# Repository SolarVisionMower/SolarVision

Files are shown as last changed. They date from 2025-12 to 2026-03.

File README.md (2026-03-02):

# SolarVision Mower

> [!NOTE]
> *This project is still in development!*

## Project Overview

SolarVision Mower is a YOLO and LiDAR based autonomous lawnmower that we're building for our final capstone engineering project. Once complete, it will feature *fully custom hardware and software*, which includes custom circuitry, firmware, 3D printed or welded components, a modified frame from an existing TORO lawnmower, and much more.

To stay up-to-date with the latest developments, check out the [dev/general][01] branch (specifically the [BACKLOG.md][02] file), to find a detailed list of everything we're doing. It will also help to navigate the various branches and directories (which will most likely grow in complexity as time progresses). Branches will the naming convention `xx/yy` are *permanent* branches, in the category specified by `xx`. Others can be considered temporary only.

## Tech Stack

- Software Tools
    - **KiCAD** - For PCB Design
    - **Fusion360** - For designing 3D models
    - **ESP-IDF** - For firmware programming on the ESP32
    - **STM32CubeMX** - For hardware configuration and initial code generation on the STM32
    - **STM32CubeIDE** - For firmware programming on the STM32
    - **ST Edge AI Suite** - For YOLO model conversion and code generation
- Software Libraries
    - **FreeRTOS** - For multithreading on both microcontrollers
    - **[espressif/arduino-esp32][05]** - For running Arduino functions in the ESP32
    - **[thijses/rplidar][06]** - For ease of integration of the RPLidar A1.
    - **[jh247247/DW1000-fan-video][07]** - Initial firmware implementation for the Ultra Wideband Positioning Modules
- Hardware Tools
    - Fabrication tools from the [NJIT Makerspace][08].
    - Circuit analysis tools from the [NJIT ECE Labs][09].
    - SLogic16U3 Logic Analyzer.
    - [JLCPCB][10] for PCB fabrication

## The Team

- Arnav Revankar
    - **Computer Engineer** - Graduating Dec 2026
    - Responsibilities:
        - Co-Lead Developer, and Manager for Hardware Design.
        - Developed the [STM32N6 Board][03]
        - Oversaw the development of the [Main Board][04]
- Panuha Were
    - **Computer Engineer** - Graduating May 2026
    - Responsibilities:
        - Co-Lead Developer, and Manager for Software Design
        - Contributed to the [Main Board][04] hardware design
        - Overseeing Firmware Development for the ESP32S3
- Layth Younes 
    - **Computer Engineer** - Graduating May 2026
    - Responsibilities:
        - Developer, and Manager for 3D Designs and Fabrication
        - Contributed to the [Main Board][04] hardware design
        - Overseeing the physical design of the frame, and enclosures.
- Daniel Assaf
    - **Computer Engineer** - Graduating May 2026
    - Responsibilities:
        - Developer, and Test/Integration Engineer
        - Contributed to the [Main Board][04] hardware design
        - Contributed to writing Documentation/Reports on progress.

## License

As of date (March 2nd, 2026) we have *not* decided upon a license. All rights are reserved by the authors.

<!-- Links -->
[01]: https://github.com/SolarVision/SolarVisionMower/tree/dev/general
[02]: https://github.com/SolarVision/SolarVisionMower/blob/dev/general/docs/BACKLOG.md
[03]: https://github.com/SolarVision/SolarVisionMower/tree/dev/PCBDesign/Hardware/STM32N6_Board
[04]: https://github.com/SolarVision/SolarVisionMower/tree/dev/MainBoard/Hardware/Main_Board
[05]: https://github.com/espressif/arduino-esp32
[06]: https://github.com/thijses/rplidar
[07]: https://github.com/jh247247/DW1000-fan-video
[08]: https://njitmakerspace.com
[09]: https://ecelabs.njit.edu
[10]: https://jlcpcb.com

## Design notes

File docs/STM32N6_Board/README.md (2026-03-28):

# STM32N6 Board

Documentation for all components to be used on the board.

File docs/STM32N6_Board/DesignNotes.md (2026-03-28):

# Design Notes

## Ballout

- This section was completed *after* wiring the Power and Analog units, as well as the NOR Flash unit in the schematic. However it is important, so it'll be at the top.
- There's a spreadsheet for the BGA pinout, can be found [here](https://docs.google.com/spreadsheets/d/1W3wl7rZQ2mxVOFGO9Ns9zJrD_qd8Au_sG3PKxmy8APU/edit?usp=sharing). It has *all* the balls, but the ones we need have been checked off, and most have signals labeled next to them.
- The pinout was generated in STM32CubeMX, and the configuration has been stored in [`Software/`](../../Software).
- The ballout from the CubeMX's UI is shown below. It isn't very detailed in the photo, so consulting the spreadsheet (or better, git pull and open in CubeMX) is highly recommended.

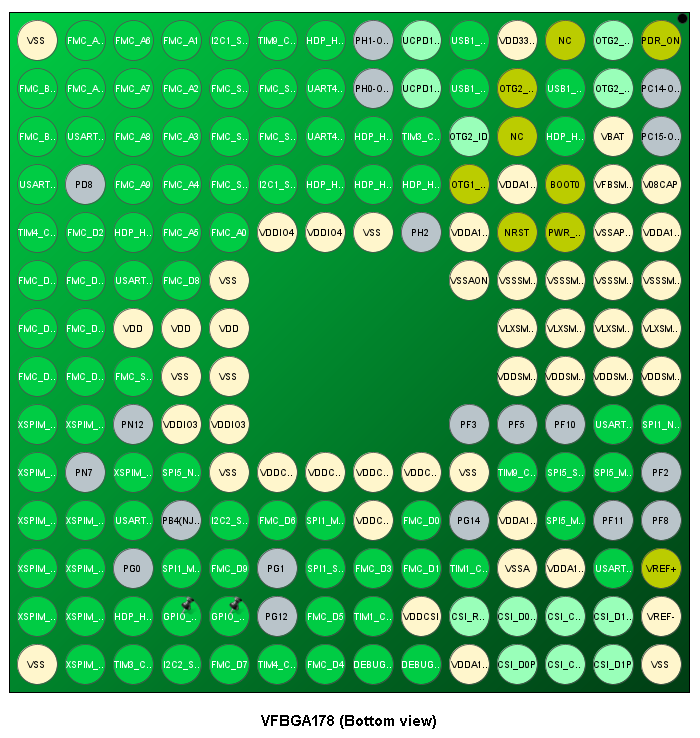
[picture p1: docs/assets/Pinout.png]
Ballout from STM32CubeMX


The STM32's **connection with the main board** will be through a set of two 18 pin header pins on each side of the stm32. These pins will be as follows, top to bottom:

| Left | Right |
|:----:|:-----:|
| 5V | 5V |
| GND | GND |
| UART1-TX | UART2-TX |
| UART1-RX | UART2-RX |
| UART3-TX | UART4-TX |
| UART3-RX | UART4-RX |
| SPI1-MISO | SPI5-MISO |
| SPI1-MOSI | SPI5-MOSI |
| SPI1-CS | SPI5-CS |
| SPI1-CLK | SPI5-CLK |
| I2C1-SDA | I2C2-SDA |
| I2C1-SCL | I2C2-SCL |
| TIM1-CH1 | TIM3-CH2 |
| TIM1-CH2 | TIM3-CH3 |
| TIM4-CH1 | TIM9-CH1 |
| TIM4-CH2 | TIM9-CH2 |
| 5V | 5V |
| GND | GND |

- Putting 5V *and* ground on each side promotes better current flow through the ground planes I believe. This will allow charges to flow in the direction to the nearest ground.
- 5V pins will have reverse polarity protection diodes.
- All pins are technically GPIO pins, but they can also be used specifically for the tasks displayed. The timer pins are capable of PWM, and analog read upto 1v8.

## Power

- VDD has 7 capacitors because:
    - 3 VDD pins
    - 2 VDDIO3 pins
    - 2 VDDIO4 pins
- VDDCORE has 6 capacitors because:
    - 5 VDDCORE pins
    - 1 VDDCSI pin
- VDDA1V8 has 4 capacitors because:
    - ADC, CSI, USB, and PLL power
- ***NOTE:*** In PCB design, keep decoupling capacitors close to the BGA chip.

- Notes on Power Pinout:
    - Will obviously need a ground pin or two
    - Input voltage pin will be 5V, with a max of 3A consumption (Buck converter on main board). Use IPC-2221 to determine trace widths. 
        - The hardware development AN suggests using a 4 (if not 6) layer PCB with the inner layers being strictly ground and power planes.
    - V\_DD and V\_DDA18AON ***need to start first*** according to the boot order. The rest of the pins can be powered after. Thus:
        - V\_DD and V\_DDA18AON must be powered off two *separate* (crucial for analog signal integrity) LDO's.
        - V\_DDA1V8 will then be powered by an LDO off of the 5V input, *with PWR\_ON on the enable pin*.
        - V\_DD1V8 and V\_DD3V3 should be powered by buck converters off 5V for high power. Again *PWR\_ON TO ENABLE PIN*.
    - V\_DDA1V8PMU is powered off V\_DD1V8, with 50R@100MHz ferrite and 100n bypass cap in between.

## Analog Unit

- USB:
	- DP and DM are differential pairs, with 90 Ohms between them, or 45 Ohms each between them and ground.
	- Length matching within a pair should be within 2mm, and maximum trace length no longer than 200mm.
	- Ideally route DP and DM over a ground plane.
	- Using the ECM42-40A100N6 to filter noise.
	- Both CC pins have been pulled down. To change configuration, unsolder R24 or R25.
	- USB Power Details:
		- When connected to a host via USB C, VBUS will be able to power 5V via the diode D5. 
		- When *acting* as a USB host (`EN = 1`), the NMOS will enable VBUS to be powered by 5V.
		- If connected to a host, but also powered by 5V rail, VBUS and 5V will be powered separately, *but to the same voltage*, so theoretically I\_D should be 0.
		- Same situation as above if acting as a host, and for some reason a device supplies 5V on VBUS
		- If, for any reason, there's a flaw in this design, **unsoldering D5** should fix it, but external powering capabilities will vanish.
- CSI
	- The 3 pairs of P and N pins for the CSI peripheral are also *differential pairs*. There's 100 Ohms impedance between them, and 50 Ohms between each of them and ground.
	- Length matching within a pair must be within 0.1mm, and between clock and data pairs 2.5mm.
	- Route over a ground plane.
	- Trace lengths must not exceed 200mm.
- General
	- NRST is internally pulled up via 40k Ohms. Thus, the button debouncing cap will have a H-L time constant of 1ms, and L-H of 4ms.
	- NRST will also be connected to a GPIO, which one is to be determined.

## XSPI NOR Flash

- Pin configurations
	- Uses pins PN[0..12]
	- CS is active low, on pin PN1
	- CLK is on PN6
	- DQS (Data Strobe) is on pin PN0
	- Serial IO pins are on PN[2..5] and PN[8..11]
	- 3V supply by separate LDO using label VDD_OCTO
- Capacitors should be placed close to supply pins, in pairs of 4.7u and 100n.
- SIO pins to be length matched to within 10mm (I say 1-5mm), and impedance matched to 50 Ohms between trace and ground.
- Differential pairs must have trace impedance of 100Ohms between them.
- Trace capacitance not to exceed 20pF, and trace length not to exceed 120mm (use resistor termination otherwise; not doing this).
- External push button to reset the Flash. Once development is complete, R28 can be unsoldered to prevent accidentally deleting data.
- NRST connected to the reset button through a diode.

## PCB Design

- Impedance controlled traces:
	- For 50 Ohms single ended, 0.1565mm
	- For 45 Ohms single ended, 0.1933mm
	- For 100 Ohms diff pair, 50 Ohms single ended, 0.15mm wide, 0.5mm spacing, > 2mm gap to ground plane
	- For 90 Ohms diff pair, 45 Ohms single ended, 0.19mm wide, 0.5mm spacing, > 2mm gap to ground plane

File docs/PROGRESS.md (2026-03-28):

# PROGRESS

Documentation of all development across all branches.

[Link to BACKLOG.md](./BACKLOG.md)

> [!NOTE]
> Upon merging a development branch into this branch (`dev`), update the Completed section with the latest developments,
> and *in the proper format!* This format is `<Completed Task> - <Merged By> - <Date> - <Commit Hash>`

## TODO

- **Physical Design**
	- Designing the Frame
	- Welding the Frame
	- Attaching and Testing Components
	- Building the Battery
- **PCB Design**
	- Main Board Design
	- Power Board Design (TBD)
	- STM32N6 Board Design
- **Programming**
	- Preliminary ESP32 Programming (FreeRTOS)
	- Interfacing ESP32 with LiDAR + UWB
	- Model Conversion and C Code Generation
	- Preliminary SLAM Code Testing
	- Path Planning Code Testing
	- Mower State Monitor on RbPi

## IN PROGRESS

- **PCB Design**
	- STM32N6 Board Design
		- Added all footprints, and symbols for MX25LM, IS42, and STM32
		- Added symbols for SPX5205 LDO, and MC34064 Buck. Standard footprints.
		- Completed Power and Analog Units of schematic, as well as MX25LM NOR Flash
		- Completed pinout process in STM32CubeMX. Completed pinout is [here](https://docs.google.com/spreadsheets/d/1W3wl7rZQ2mxVOFGO9Ns9zJrD_qd8Au_sG3PKxmy8APU/edit?usp=sharing).
		- Completed schematic layout, ERC check, and footprint assignment. Next is PCB layout.

## COMPLETED

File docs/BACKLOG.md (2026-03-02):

# BACKLOG

> [!IMPORTANT]
> Try not to commit to this branch! Commit in one of the sub-branches (ie `dev/xyz`) and merge as necessary

## Links to Branches

- [dev/PhysicalDesign](https://github.com/SolarVisionMower/SolarVision/tree/dev/PhysicalDesign)
- [dev/PCBDesign](https://github.com/SolarVisionMower/SolarVision/tree/dev/PCBDesign)
- [dev/DataCollection](https://github.com/SolarVisionMower/SolarVision/tree/dev/DataCollection)
- [dev/Programming](https://github.com/SolarVisionMower/SolarVision/tree/dev/Programming)
- [dev/Testing](https://github.com/SolarVisionMower/SolarVision/tree/dev/Testing)
- [dev/Shed](https://github.com/SolarVisionMower/SolarVision/tree/dev/Shed)
- [dev/Redocking](https://github.com/SolarVisionMower/SolarVision/tree/dev/Redocking)

## Major Tasks

Detailed list of everything to be done, in chronological order. It should be as detailed as possible; update here and in [PROGRESS.md](./PROGRESS.md) if anything's missing.

<details>
<summary>Physical Design</summary>

Design and build of the mower's frame; all development will be in the `dev/PhysicalDesign` branch.

As of Jan 17th 2026, we have yet to discuss details about the physical design. However, the general outline will be as follows:

- Begin with a base mower, and weld/rivet on L-bracket extensions on all four corners
- On top of L-bracket posts, weld more L-brackets to form a rectangular shape
- On top of the created base, mount aluminum extrusions as needed, and weld extensions for the wheels and rear motors. [Here is some inspiration](https://youtube.com/shorts/RLpBBrU3Dhs).
- Once electronics is complete, design and 3D print enclosures for the electronics.

Along with this, we will need to build a 10S 4P battery pack out of 18650 batteries. There is also the option of purchasing a pre-built battery, but that choice will come down to cost-balance, and is yet to be discussed (01/19/2026).
</details>

<details>
<summary>PCB Design</summary>

> [!IMPORTANT]
> Please place ***ALL DOCUMENTATION*** (datasheets, reference manuals, etc.) in their respective folders under the `docs` directory.
> All designs must be based off previous designs or specs from datasheets.

All development should be in the `dev/PCBDesign` branch.

There are 3 boards which we will need to design, order, and assemble:

- STM32N6 Board
    - This will be a 4 layer board, designed in KiCAD.
    - Will use an **STM32N657I0H3Q**
        - VFBGA178 Ballout
        - 0.8mm Pitch
        - 106 I/Os (not all used; perhaps only 20, others in internal pull-down state)
        - Comm Protocols we will use:
            - UART, for communication with the ESP32
            - I2C and SPI, for collecting sensor data
            - MIPI CSI-2, for camera connection
            - XSPI, for interfacing Macronix MX25LM51245GXDI00 NOR Flash (used for boot and binary storage), same as [the Nucleo-144 board](https://www.st.com/resource/en/schematic_pack/mb1940-n657x0q-c02-schematic.pdf)
            - (*IF TIME PERMITS*) FMC_SDRAM16, for interfacing IS42S16800F-7TLI SDRAM chip, to store YOLO weights. Otherwise, use system memory with YOLOv8-nano.
            - (*IF TIME PERMITS*) FMC Display Interface, for on-board monitoring. Not needed at all, since we'll have the web-UI.
        - Of the above, CSI, XSPI, and FMC_SDRAM will have dedicated connectors on the board, while the rest will have header pins to connect to the main control board.

- Main Control Board
    - This board will house the STM32N6 board, as well as an ESP32 S3, UWB Tag, and 433MHz RF module. MCU boards connected via header pins.
    - It will be a 2-layer board for simplicity
    - Will also house LDO regulators to deliver 1.8, 3.3, and 5V respectively, powering the ESP32 and STM32
    - Within the board:
        - Route UART between the boards
        - Route *all* ESP32 pins to the main board's header pins
        - Route I2C, SPI, FMC Display, and few extra I/O pins (TBD) from STM32 to the main board's header pins

- Power Board
    - ***NOTE:*** Necessity of this board is up to debate, as off-the-shelf power components are already available, and there's an added risk of errors in our designs. **TO BE DISCUSSED (01/19/2026)**
    - This board will power the **motors, lights, and other high-power electronics**
    - This board shall have *no MCU*; all control goes directly from main board to power board.
    - Connection to main board will be through either ribbon cable, or unseparated header pin cables (resembles ribbon cable)
</details>

<details>
<summary>Data Collection/Training</summary>

> [!NOTE]
> Since this is a *software* related portion of the project, try to use dockerized tools, if applicable

All development will be in the `dev/DataCollection` branch.

The YOLOv8 model running on the STM32 will be a fine-tuned segmentation model. Our goal is that it'll be able to detect grass vs non-grass, based on input from the camera. In order to do this, we must *collect training data*, and then *train* the model on a GPU. Current plan is as follows:

- Collect 300 to 400 images of a lawn, from a camera 2 feet in the air, parallel with the earth.
- Manually annotate all the images using Label Studio
- Load dataset into Google Colab, write training script, and train for ~100 epochs.
- Export model to `pt`, use PyTorch to quantize to INT8, and export to ONNX
- Finally, utilize ST Edge AI Core to [generate C code](https://stm32ai-cs.st.com/assets/embedded-docs/stneuralart_getting_started.html), then compile in STM32Cube IDE and flash.
- Test model accuracy
</details>

<details>
<summary>Programming</summary>

> [!NOTE]
> Since this is a *software* related portion of the project, try to use dockerized tools, if applicable.
> Also, try to write *modular* code, which can be improved upon at any instance.

All development will be in the `dev/Programming` branch.

Below is how we anticipate control flow within our entire project:

- STM32
    - Camera frame is captured and processed, creating segmented frame.
    - Mask of mower's current trajectory is mapped onto the segmented frame. 
    - Finally, logic (that we've yet to define) determines distance to the lawn's boundary, if applicable.
    - Results are sent to the ESP32 via UART
    - Mower state received from ESP32 is then displayed on FMC display, or sent to Raspberry Pi base station using the 433MHz RF module.
- ESP32
    - Utilize FreeRTOS for multithreading
    - ESP32 receives distance-to-boundary predictions, and replies with the current state of the mower:
        - Position, Speed, trajectory (steering angle), Blade motor RPM, and power consumption (if possible)
        - Sent using CSV format over UART
        - Parity checker to ensure data's integrity
    - Collects sensor data from LiDAR and UWB/GPS (preferably UWB Trilateration, from other open source projects), and integrates into SLAM system.
- SLAM
    - This portion is still slightly TBD
    - Keep track of mower's position, and update in an infinite loop.
    - At beginning of mowing cycle, use path-planning algorithm to set up waypoints at boundaries of the lawn. 
    - Travel to waypoints, simultaneously updating SLAM location and map. Once boundary is detected, turn around and drive back.
- Web-UI
    - Raspberry Pi base station will run a web server and API endpoint using Python, or some other tool, TBD.
</details>

<details>
<summary>Testing</summary>

All development will be in the `dev/Testing` branch (if necessary).

This will include testing of the following (if not already done, should be already done actually):

- Motors:
    - Make sure motors run, and the ESP32 can control them as designed.
- Vision System
    - Make sure the STM32 is able to receive data from the CSI camera, is able to process it, and generate accurate results. This is crucial
- LiDAR System
    - Make sure the ESP32 is able to receive data from the LiDAR sensor, and is able to process it into the SLAM map
- UWB Positioning System
    - Make sure it can calculate position based on distance from 2 anchors. 
    - Make sure it can process current position into SLAM model.
- SLAM
    - Make sure SLAM is effectively able to update its map and position, and send commands in order to reach waypoints, in a perpetual loop.
</details>

<details>
<summary>Shed Building</summary>

All development will be in the `dev/Shed` branch.

At this point, we will know the dimensions of the mower, and will be able to construct the shed. General steps will be:

- Build/buy shed
- Install solar panels
- Install MPPT charge controller with lead acid batteries
- Permanently install Raspberry Pi Base Station, and UWB anchors.
</details>

<details>
<summary>Re-docking Programming</summary>

All development will be in the `dev/Redocking` branch.

(*IF TIME PERMITS*)

Add functionality to the code to be able to detect and return to the docking station.
</details>

## Timeline

There are 4 of us team members, and so we will be splitting up responsibilities, setting deadlines, and holding each other accountable for said deadlines. Which team member performs which tasks has not been decided yet (01/19/2026), and thus they are referred to as Member #1, #2, #3, and #4 until we have reached a consensus. Roles have been distributed as evenly as possible.

[Budgeting spreadsheet can be found here.](https://drive.google.com/drive/folders/1ZBdfXEnTgUfjmxBh2aHWwEIxdO-Y8bWZ?usp=sharing)

**Edit (01/24/2026):** We have reached a consensus on the division of responsibilities. The Gantt Chart we created can be [found here](https://docs.google.com/spreadsheets/d/1--nTUD_fsUKMP01lJ4NdwEQdVoJq4U2uNLm4wrHddHY/edit?usp=sharing).

<!--
Table Template

| Task | Member \# | **Deadline** |
|:----:|:---:|:---:|
|  |  |  |
-->

- **Physical Design**

| Task | Member \# | **Deadline** |
|:----:|:---:|:---:|
| Welding the Frame | 1 | Feb 1 |
| Attaching physical components | 1 | Feb 8 |
| Testing DC Motors, and mower function | 1 | Feb 8 |
| Designing and 3D printing enclosures | 2 | TBD |
| Designing and Building 10S4P 18650 Battery | 1 | Feb 15 |

- **PCB Design**

| Task | Member \# | **Deadline** |
|:----:|:---:|:---:|
| Main Board Design, Validate, and Order | 2 | Feb 1 |
| Power Board Design, Validate, and Order (TBD) | 2 | Feb 8 |
| STM32N6 Board Design, Validate, and Order | 3 | Feb 1 |

- **Data Collection/Training**

| Task | Member \# | **Deadline** |
|:----:|:---:|:---:|
| Collecting Pictures | 3 | Feb 4 |
| Preliminary Training | 3 | Feb 11 |
| Testing/Iterations | 3 | Feb 21 |

- **Programming**

| Task | Member \# | **Deadline** |
|:----:|:---:|:---:|
| Preliminary ESP32 Programming (FreeRTOS) | 4 | Feb 1 |
| Interfacing ESP32 with LiDAR + UWB | 4 | Feb 8 |
| Model Conversion and C code generation | 4 | Feb 18 |
| C code assimilation + YOLO testing on N6 | 3 | Feb 21 |
| Preliminary SLAM Code Testing | 2 | Feb 28 |
| Path planning code testing | 2 | March 7 |
| Mower State Monitor on RbPi | 1 | Feb 28 |

- **Testing**

| Task | Member \# | **Deadline** |
|:----:|:---:|:---:|
| Testing Physical Components | 1 | March 7 |
| Testing ESP32 | 2 | March 14 |
| Testing STM32 | 3 | March 7 |
| Testing Communication, Web-UI, and overall mower function | 1, 2, 3, 4 | March 25 |

- **Shed Building**

| Task | Member \# | **Deadline** |
|:----:|:---:|:---:|
| Constructing Shed | 4 | April 1 |
| Installing Solar Panels | 4 | April 7 |
| **Senior Design Showcase Qualifications** | -- | April 7 |
| Installing MPPT Charge Controller, stationary battery pack, and mower charger | 4 | April 14 |

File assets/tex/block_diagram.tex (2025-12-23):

\usepackage{extarticle}
\documentclass[14pt]{extarticle}
\usepackage[paperheight=7in, paperwidth=10in, total={9.5in, 6.5in}]{geometry}
\usepackage{tikz}

\usetikzlibrary{automata, positioning, shapes.geometric, arrows.meta}

\tikzset{
    state/.style={
        ellipse, draw, fill={rgb:black,1;white,5},
        minimum size=10pt
    },
    box/.style={
        rectangle, draw, fill={rgb:black,1;white,5},
        minimum width=75pt, minimum height=50pt, align=center,
        anchor=north
    },
    mm/.style={
        -{Stealth[length=3mm]}
    },
    oo/.style={
        {Stealth[length=3mm]}-{Stealth[length=3mm]}
    },
    tikkup/.style={
        anchor=south west, rotate=20, align=left
    },
    tikkdown/.style={
        anchor=north east, rotate=20, align=right
    }
}

\begin{document}

\begin{center}
    {\Huge \bf Block Diagram of Autonomous Lawnmower} \\[45pt]
    \begin{tikzpicture}[x=5pt, y=5pt]
        % \draw[help lines, step=5] (0,0) grid (130,90);
        % \node at (0,0) {O};
        
        \node[box, minimum height=200pt, minimum width=125pt]   (mcu)           at (65,60) {STM32N6 MCU\\for YOLO Inference\\\\and\\\\ESP32 S3\\SLAM pathfinding\\and system control};

        % Navigation system
        
        \node[box] (autonomous)    at (35,65) {Autonomous\\Navigation\\System};
        \node[box] (gps)           at (10,65) {GPS/RTK\\Module};
        \node[box] (lidar)         at (10,80) {LiDAR\\Module};
        \node[box] (computer)      at (35,80) {Camera};

        \path (autonomous) edge[mm, out=0, in=180] (52,50)
                (gps) edge[mm] (autonomous)
                (lidar) edge[mm] (autonomous)
                (computer) edge[mm] (autonomous);

        % Blade speed control

        \node[box] (speedcontrol)   at (95,65)  {Blade Speed\\Control (PID)};
        \node[box] (speedsensor)    at (95,80)  {Blade Speed\\Sensor};
        \node[box] (blademotor)     at (120,65) {Blade Motor};

        \path (85,58) edge[mm, out=180, in=0] (78,48)
                (78,52) edge[mm, out=0, in=180] (85,62)
                (speedcontrol) edge[mm] (blademotor)
                (speedsensor) edge[mm] (speedcontrol);

        % Mower height control

        \node[box] (heightcontroller)   at (95,45)  {Mower Height\\Motor Controller};
        \node[box] (heightmotor)        at (120,45) {Mower Height\\Motor};

        \path (78,40) edge[mm] (heightcontroller)
                (heightcontroller) edge[mm] (heightmotor);

        % RF Modules

        \node[box] (transmitter)    at (95,25)  {RF Module};

        \path (78,28) edge[mm, out=0, in=180] (87,18)
                (87,22) edge[mm, out=180, in=0] (78,32);

        % Motors and Motor Controllers

        \node[box] (leftcontrol)    at (35,45) {Left Motor\\Controller};
        \node[box] (leftmotor)      at (10,45) {Left Motor};
        \node[box] (rightcontrol)   at (35,25) {Right Motor\\Controller};
        \node[box] (rightmotor)     at (10,25) {Right Motor};

        \path (52,40) edge[mm] (leftcontrol)
                (leftcontrol) edge[mm] (leftmotor)
                (52,30) edge[mm, out=180, in=0] (rightcontrol)
                (rightcontrol) edge[mm] (rightmotor);
    \end{tikzpicture}
\end{center}
    
\end{document}

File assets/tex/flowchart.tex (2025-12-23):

\usepackage{extarticle}
\documentclass[14pt]{extarticle}
\usepackage[paperheight=8.7in, paperwidth=11in, total={10.5in, 8.2in}]{geometry}
\usepackage{tikz}

\usetikzlibrary{automata, positioning, shapes.geometric, arrows.meta}

\tikzset{
    state/.style={
        ellipse, draw, fill={rgb:black,1;white,5},
        minimum size=10pt
    },
    mm/.style={
        -{Stealth[length=3mm]}
    },
    oo/.style={
        {Stealth[length=3mm]}-{Stealth[length=3mm]}
    },
    tikkup/.style={
        anchor=south west, rotate=27, align=left
    },
    tikkdown/.style={
        anchor=north east, rotate=27, align=right
    }
}

\begin{document}

\begin{center}
    {\Huge \bf Flowchart for Project Completion} \\[15pt]
    \begin{tikzpicture}[x=5pt, y=5pt]
        %\draw[help lines, step=5] (0,-30) grid (130,65);
        
        \node[state] (start)        at (65,60) {Start};
        
        \node[state] (SolarShed)    at (30,50) {Solar Shed};
        \node[state] (Shed)         at (10,40) {Shed};
        \node[state] (SolarPanel)   at (45,40) {Solar Panel};
        \node[state] (Battery)      at (15,23) {Battery};
        \node[state] (BMS)          at (45,23) {BMS};
        
        \node[state] (SystemBench) at (95,50) {System Bench-Test};

        \node[state] (Lidar)        at (70,40) {Lidar};
        \node[state] (GPS)          at (95,40) {GPS/RTK};
        \node[state] (YOLO)         at (120,40) {YOLO};
        % \node[state] (Triangle)     at (120,40) {Triangulation};

        \node[state, align=center] (Interface1)     at (70,23) {Interface\\w/ STM32};
        \node[state, align=center] (Interface2)     at (95,23) {Interface\\w/ STM32};
        \node[state, align=center] (Interface3)     at (120,23) {Interface\\w/ STM32};

        \node[state, align=center] (Navigation) at (95,7) {On-board ESP32 S3\\for Navigation};

        \node[state, align=center] (physical) at (35,7) {Physical Design\\+ Reiterations};

        \node[state] (complete) at (65,-5) {Completed Project};

        \path (start) edge[mm, out=180, in=30] (SolarShed)
                (SolarShed) edge[mm, out=180, in=90] (Shed)
                (SolarShed) edge[mm, out=0, in=90] (SolarPanel)
                (SolarPanel) edge[mm, out=180, in=90] (Battery)
                (SolarPanel) edge[mm] (BMS)
                (start) edge[mm, out=0, in=150] (SystemBench)
                (SystemBench) edge[mm, out=-180, in=90] (Lidar)
                (SystemBench) edge[mm] (GPS)
                (SystemBench) edge[mm, out=0, in=90] (YOLO)
                %(SystemBench) edge[mm, out=0, in=90] (Triangle)
                (Lidar) edge[mm] (Interface1)
                (GPS) edge[mm] (Interface2)
                %(Triangle) edge[mm] (Feasible)
                %(Feasible) edge[mm, line width=2pt, dash pattern={on 6pt off 4pt}, out=-90, in=20] (Navigation)
                (YOLO) edge[mm, out=-90, in=90] (Interface3)
                (Interface3) edge[mm, out=-90, in=0] (Navigation)
                (start) edge[-, out=-120, in=90] (58,40)
                (58,40) edge[-, out=-90, in=90] (58,25)
                (58,25) edge[mm, out=-90, in=45] (physical)
                (physical) edge[mm, out=-90, in=180] (complete)
                (Navigation) edge[mm, out=-90, in=0] (complete)
                (Interface1) edge[mm, out=-90, in=180] (Navigation)
                (Interface2) edge[mm] (Navigation)
                (BMS) edge[mm, out=-90, in=90] (physical)
                (Battery) edge[mm, out=-90, in=170] (physical)
                (Shed) edge[-, out=-130, in=90] (5,25)
                (5,25) edge[mm, out=-90, in=180] (physical); 

        \draw[oo] (10,-20) -- (120,-20);

        % \node at (0,0) {O};
        
        \draw[-] (15,-19) -- (15,-21);
        \draw[-] (115,-19) -- (115,-21);
        \draw[-] (27.5,-19) -- (27.5,-21);
        \draw[-] (65,-19) -- (65,-21);
        \draw[-] (40,-19) -- (40,-21);
        \draw[-] (52.5,-19) -- (52.5,-21);
        \draw[-] (90,-19) -- (90,-21);
        \draw[-] (102.5,-19) -- (102.5,-21);

        \node[tikkup] at (15,-19) {\bf Sept. 2025};
        \node[tikkup] at (115,-19) {\bf May 2025};
        \node[tikkup] at (27.5,-19) {\bf Present\\\bf Oct. 2025};
        \node[tikkup] at (65,-19) {\bf Jan. 2026};
        \node[tikkup] at (40,-19) {\bf Nov. 2025};
        \node[tikkup] at (52.5,-19) {\bf Dec. 2025};
        \node[tikkup] at (90,-19) {\bf March 2026};
        \node[tikkup] at (102.5,-19) {\bf Apr. 2026};

        \node[tikkdown] at (40,-21) {\bf Begin Solar Shed,\\\bf Battery, and BMS};
        \node[tikkdown] at (52.5,-21) {\bf Begin Bench Test};
        \node[tikkdown] at (65,-21) {\bf Begin Navigation System};
        \node[tikkdown] at (90,-21) {\bf Begin Physical Design};

        \path (102.5,-20) edge[out=-90, in=90] (108.75,-23)
                (108.75,-23) edge[out=90, in=-90] (115,-20);

        \node at (108.75,-25) {\bf Buffer Period};
    \end{tikzpicture}
\end{center}
    
\end{document}

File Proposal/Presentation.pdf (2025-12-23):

# SolarVision Mower: Autonomous Solar-Powered Lawn Maintenance

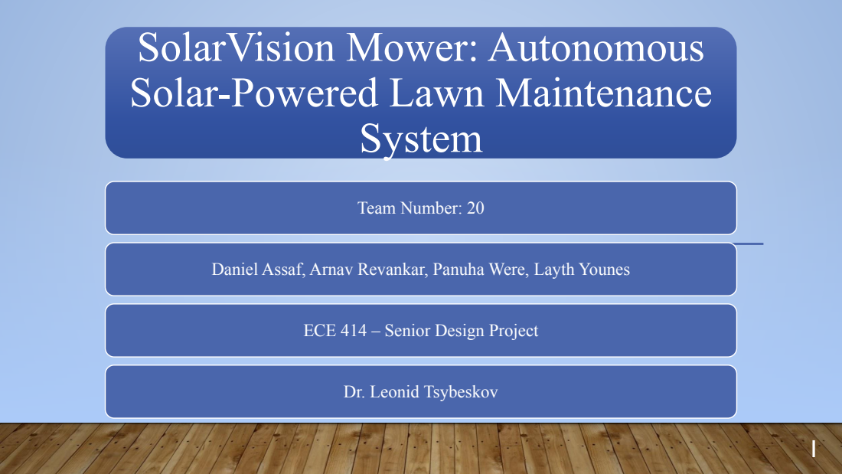
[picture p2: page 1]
System; Team Number: 20

Daniel Assaf, Arnav Revankar, Panuha Were, Layth Younes

ECE 414 – Senior Design Project

Dr. Leonid Tsybeskov

# Abstract

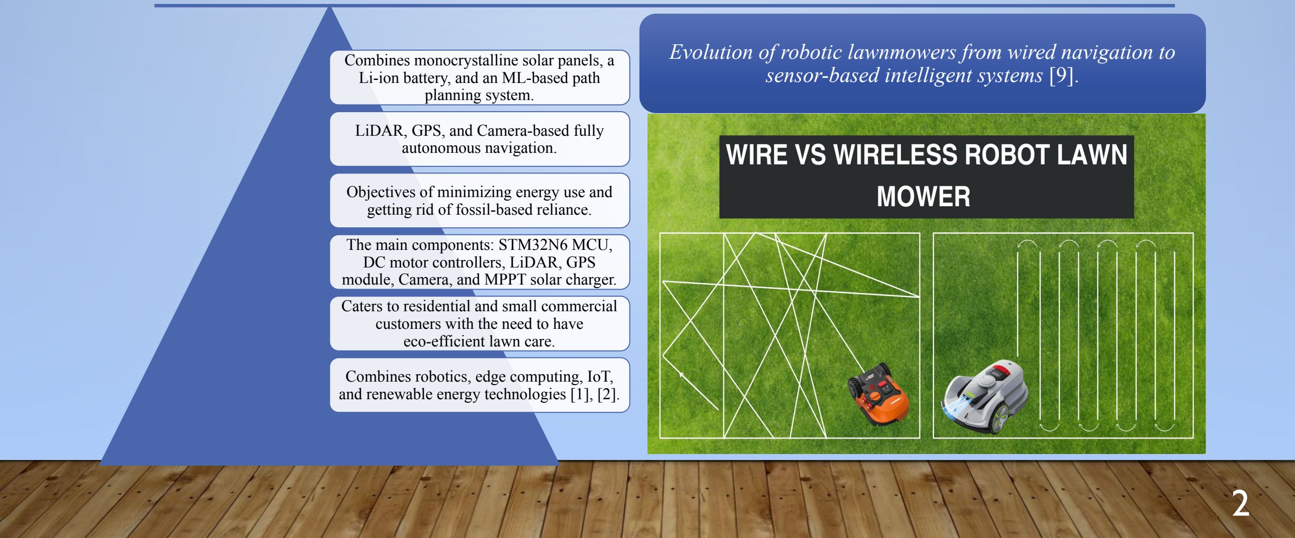
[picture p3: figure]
Combines monocrystalline solar panels, a Li-ion battery, and an ML-based path planning system.; LiDAR, GPS, and Camera-based fully autonomous navigation.; Objectives of minimizing energy use and getting rid of fossil-based reliance.; The main components: STM32N6 MCU, DC motor controllers, LiDAR, GPS module, Camera, and MPPT solar charger.; customers with the need to have eco-efficient lawn care.; Combines robotics, edge computing, IoT,; sensor-based intelligent systems [9].

Caters to residential and small commercial

and renewable energy technologies [1], [2].

## Evolution of robotic lawnmowers from wired navigation to

Part 1 Design Objectives,
Specifications, and Constraints.
- To create a completely independent solar-powered mower that can work throughout the day.

Objective 1:

- LiDAR, GPS, and Camera based SLAM
Objective 2: | obstacle avoidance and path planning
- Mobile/Web interface to monitor mower’s status and operation Objective 3:
- 3 12V monocrystalline solar panels, 36 V 10Ah Li-ion battery (10S 4P config). Power supply:
- ~1.5 hours on full charge, assuming 200W power consumption Hours of average run-time:
- Enclosure, slow control (less than 2 mph), boundary enforcement, and tilt detection. Safety limitations:
Budget constraint: | • Prototype should not go above $600.

## Proposed SolarVision Mower and its docking deck models

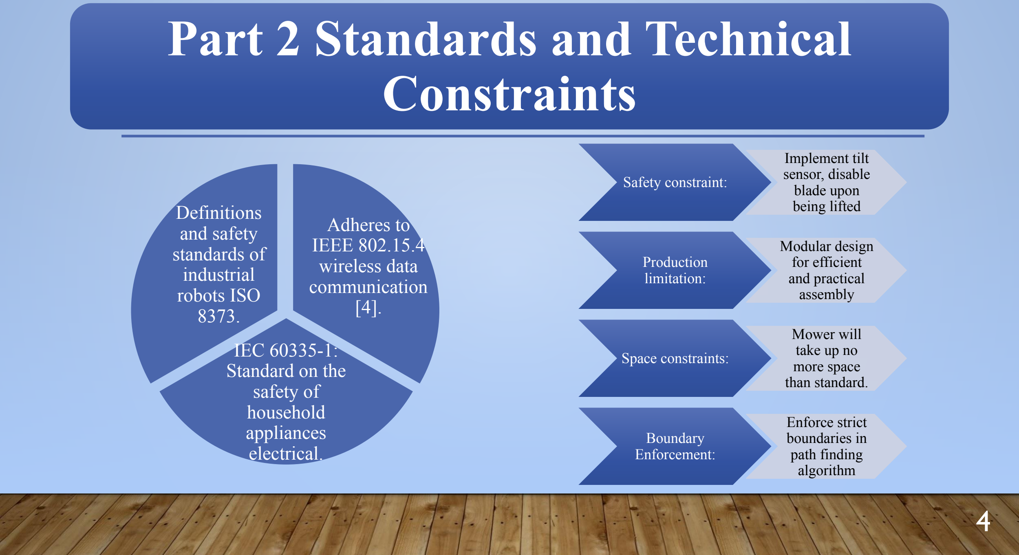
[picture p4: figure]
Part 2 Standards and Technical Constraints; Adheres to IEEE 802.15.4 wireless data communication [4].; IEC 60335-1: Standard on the safety of household appliances electrical.; Definitions and safety standards of industrial robots ISO 8373.; Safety constraint:; Implement tilt sensor, disable blade upon being lifted; Production limitation:; Modular design for efficient and practical assembly; Space constraints:; Mower will take up no more space than standard.; Boundary Enforcement:; Enforce strict boundaries in path finding algorithm

# Blocks and Components Diagram

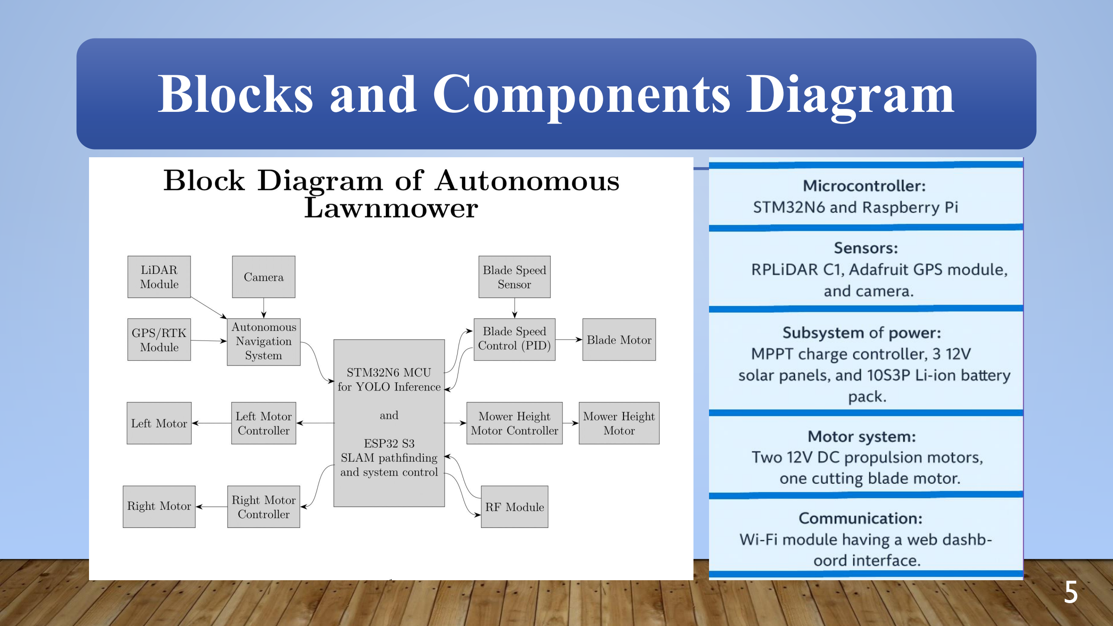
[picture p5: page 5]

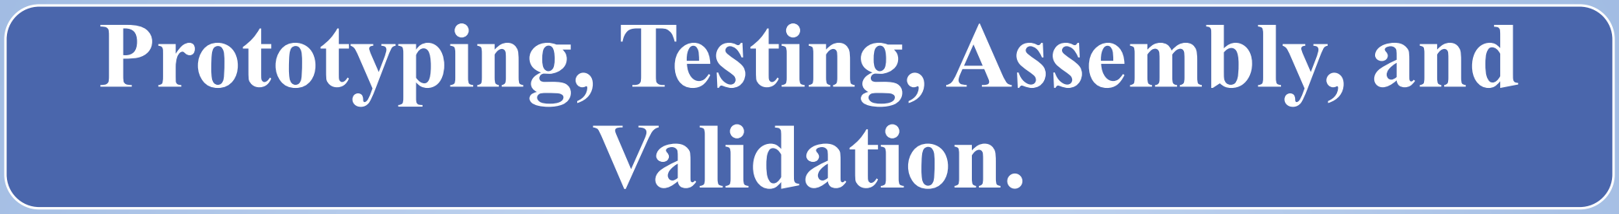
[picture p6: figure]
Prototyping, Testing, Assembly, and Validation.
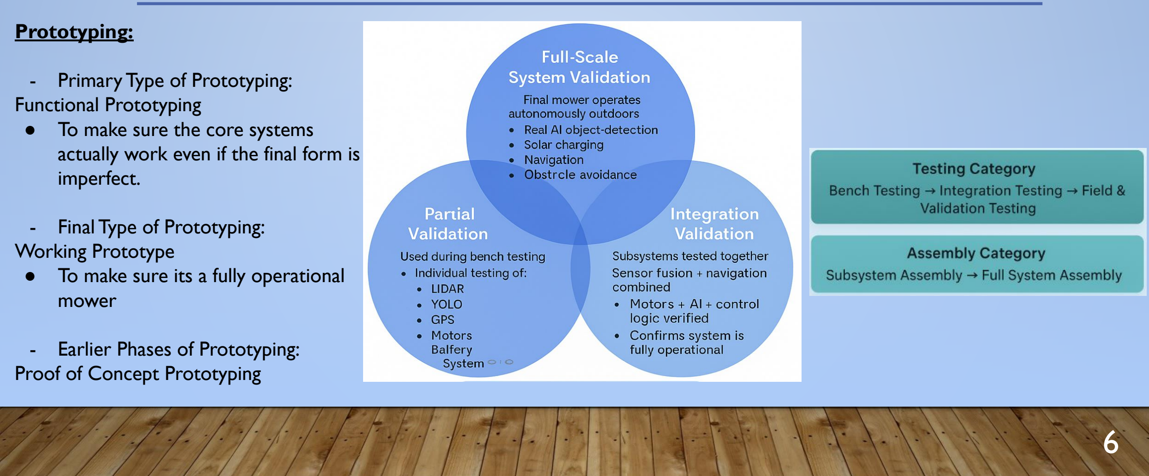
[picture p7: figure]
Prototyping:; - Primary Type of Prototyping: Functional Prototyping ● To make sure the core systems actually work even if the final form is imperfect.; - Final Type of Prototyping: Working Prototype ● To make sure its a fully operational mower; - Earlier Phases of Prototyping: Proof of Concept Prototyping

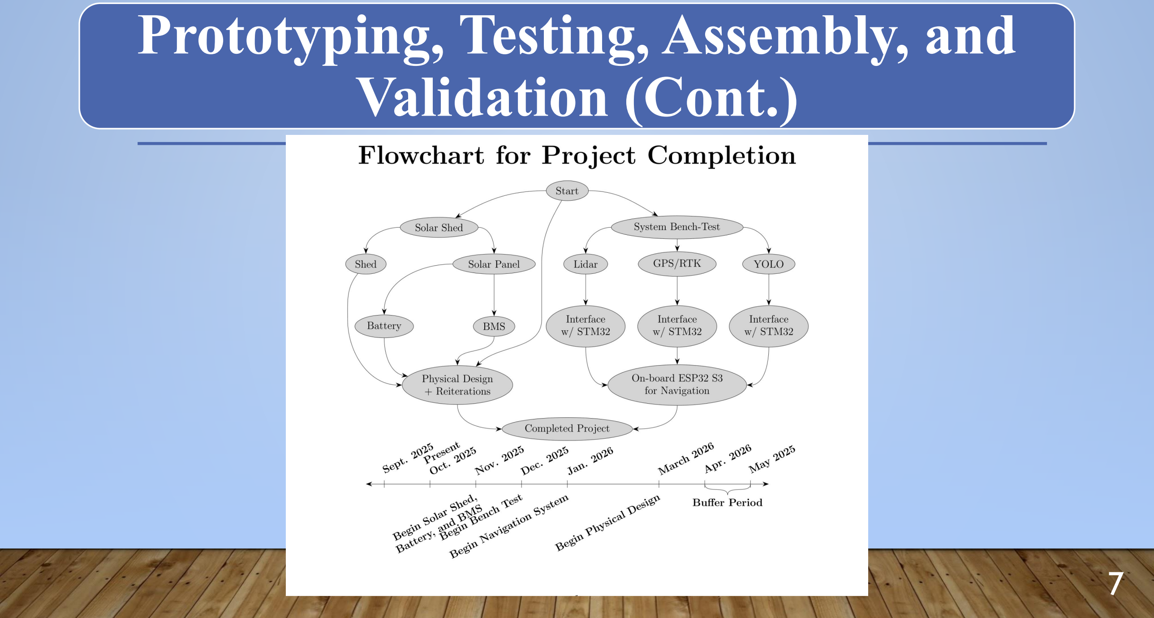
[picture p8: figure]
Prototyping, Testing, Assembly, and Validation (Cont.)

# Business, Economic Potential, and Benchmarking

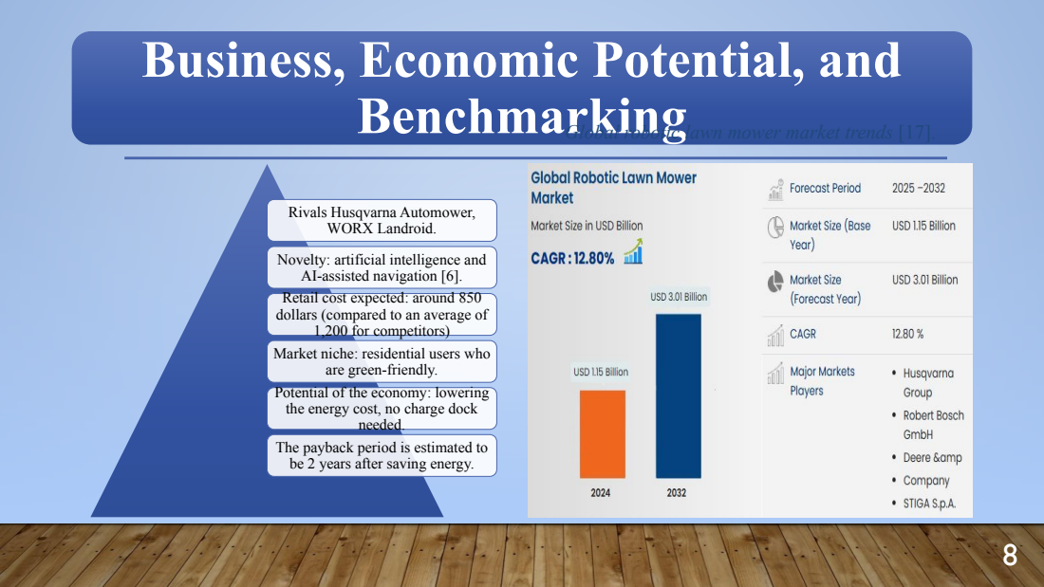
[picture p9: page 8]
needed.

Global robotic lawn mower market trends [17].

Rivals Husqvarna Automower,
WORX Landroid.

Novelty: artificial intelligence and
AI-assisted navigation [6].
Retail cost expected: around 850
dollars (compared to an average of
1,200 for competitors)
Market niche: residential users who

are green-friendly.

Potential of the economy: lowering
the energy cost, no charge dock

The payback period is estimated to
be 2 years after saving energy.

# References

A. K. Mohanty, F. Wu, M. Mincheva, et al., “Sustainable polymers,” Nature Reviews Methods Primers, vol. 2, no. 46, 2022.
G. G. N. Thushari and J. D. M. Senevirathna, “Plastic pollution in the marine environment,” Heliyon, vol. 6, no. 8, 2020.
V. E. Tartiu, R. Hurley, C. Baann, et al., “Addressing the environmental sustainability of plastics used in agriculture,” Cambridge Prisms: Plastics, vol. 3, e5, 2025.

IEEE Standards Association, “IEEE 802.15.4 Standard for Wireless Personal Area Networks (PANs),” 2020.

STMicroelectronics. “Transforming Edge AI: The power of neural processing units in modern microcontrollers”, 2025

K. Keshavarz, M. J. Alvarez, and C. J. Garcia, “The Role of Consumers in Transitioning to a Circular Economy,” Circular Economy and Sustainability, 2025.

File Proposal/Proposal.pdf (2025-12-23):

## Helen and John C. Hartmann Department of Electrical and Computer Engineering

## ECE 414 Senior Design Project Proposal

Team #: 20

Project Title: SolarVision Mower: A YOLO and LIDAR-Based Navigation System for Autonomous Solar Powered Lawnmowers

Name(s): Layth Younes | ID#: 315-846-57
Name(s): Daniel Assaf | ID#: 315-515-94
Name(s): Panuha Were | ID#: 316-697-13
Name(s): Arnav Revankar | ID#: 316-410-50

Abstract

The Solar Vision Mower is an autonomous, solar-powered mower that makes lawn care

sustainable and easy for older adults and individuals with physical disabilities. This network

combines a photovoltaic charger dock, object detection based on the YOLO model, and

LiDAR-based navigation to achieve efficient mowing without collisions. It is styled after the

Raspberry Pi or NVIDIA Jetson Nano, which is a processing unit, with the help of a

self-designed battery management system, allowing the unit to be charged independently using

solar energy. Real-time monitoring and manual override provision can be achieved using a

mobile application. Mechanical design features include Mecanum wheels and adaptive mowing

height control. The SolarVision Mower will combine renewable energy, edge computing, and

AI-based perception to reduce its environmental impact and increase accessibility. The product

will target environmentally conscious homeowners, the ageing population, and the sustainable

landscaping market to identify credible, grid-independent robotic mowing products.

Keywords: Autonomous lawnmower, solar power, YOLO object detection, LiDAR

navigation, obstacle avoidance, smart agriculture, robotic mowing systems, sustainable energy,

edge computing, and human-centered design.

Table of Contents

Introduction

Background

Autonomous outdoor service robots have emerged as one of the most promising

applications of robotics, which combine artificial intelligence (AI) and renewable energy

integration. Among these, robotic lawnmowers have gained attention in the past 3 decades.

These tools provide convenience, save time, and enhance safety as opposed to manual mowing.

The earliest robotic mowers, Husqvarna Automower, were introduced in the 1990s and

significantly improved throughout the next 2 decades [1]. These early auto-mowers relied on

perimeter wires installed around a lawn to define boundaries and guide navigation, requiring an

intensive setup [2]. They lacked sophisticated obstacle detection techniques and operated on

simple random mowing patterns. These attributes limited efficiency and adaptability.

In recent years, there have been advancements in computer vision, sensor fusion, and

renewable energy solutions. These technologies have paved the way for more intelligent,

sustainable lawn care systems. For instance, there are rapid improvements of deep learning-based

models such as YOLO (You Only Look Once) for real-time object detection [3]. Using YOLO,

robots can now identify and classify obstacles, including people, pets, or garden objects, far more

reliably than traditional rule-based approaches [3]. At the same time, Light Detection and

Ranging (LiDAR) sensors are widely used in autonomous vehicles. This technology enables

precise mapping and navigation by creating detailed three-dimensional spatial representations

[4].

Apart from sensor innovations, renewable energy has also become central to consumer

robotics. The integration of solar energy into autonomous devices is a significant energy and

sustainability solution. It offers a pathway toward reducing dependence on manual charging and fossil fuel-powered garden tools [5]. A solar-powered system ensures sustainability, reduces

operational costs, and lowers carbon emissions. This ensures alignment with the global efforts to

decarbonize small-scale machinery [6,7,8].

Figure 1: Evolution of robotic lawnmowers from wired navigation to sensor-based intelligent systems [9].

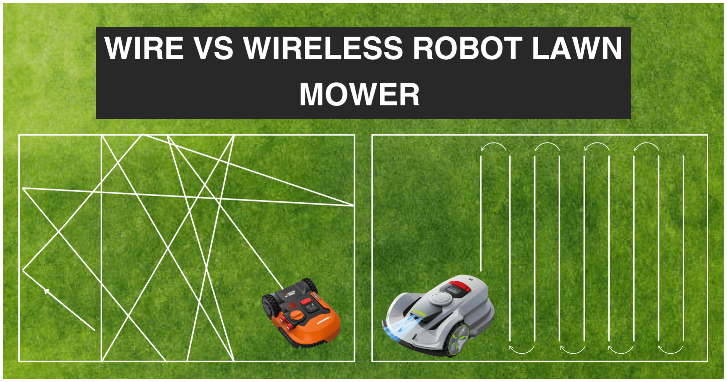
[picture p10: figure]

Problem Statement

Despite progress, existing robotic lawnmowers continue to face several limitations. As

noted earlier, many commercially available models depend on wired perimeter systems for

navigation. These systems increase installation cost and complexity [10]. Others rely solely on

GPS, which may suffer from inaccuracies in residential environments with tall buildings or dense

trees [11]. Furthermore, consumer robotic mowers typically operate on rechargeable lithium-ion

batteries that require docking at powered charging stations [12]. While efficient, these stations

rely on grid electricity, making the systems less sustainable and unsuitable for regions with

unstable energy supply.

Another issue is safety. Although robotic lawnmowers often incorporate bump sensors

and basic obstacle detection, they remain prone to accidents according to a European study that

evaluated their impact on Hedgehogs [13]. This finding implies that the mowers can harm children, pets, or fragile garden furniture. This raises ethical concerns about user safety, liability,

and the responsible deployment of autonomous garden robots.

From a market perspective, the affordability of advanced robotic lawnmowers remains a

barrier. Premium models with advanced navigation features often exceed USD 1,300 [14], while

Selvanesan et al. indicate that the price of production can be as low as USD 130 [10]. This way

of pricing hinders the accessibility of smart lawnmowers for middle- and low-income

households. For elderly users, who stand to benefit most from autonomous mowing solutions,

these cost barriers and technical setup requirements often remain prohibitive.

Our project seeks to address these issues by designing a self-sustaining, solar-powered

autonomous lawnmower. This will combine YOLO-based object detection with LiDAR

navigation for enhanced safety, precision, and sustainability. Solar charging will ensure that the

served population does not have to rely on frequent charging of the lithium-based batteries. A

model of the proposed mower is shown below.

Figure 2: Proposed SolarVision Mower and its docking deck models

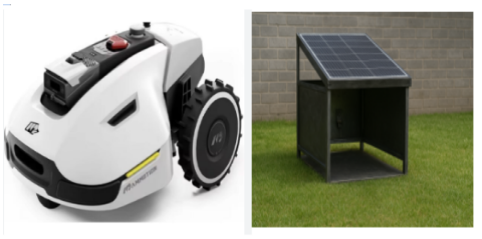
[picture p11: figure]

Objectives of the Proposed Project

Primary Objective. The main objective of the SolarVision Mower is to create a

functional prototype of an autonomous lawnmower that prioritizes sustainability, accessibility,

and intelligent navigation.

Other Objectives. Specifically, the project will aim to:

1. Develop a solar-powered charging system using a compact shed structure that allows the

mower to recharge independently, reducing reliance on grid electricity.

2. Implement YOLO-based object detection for real-time obstacle detection, ensuring safe

operation around people, pets, and objects.

3. Integrate LiDAR for accurate environmental mapping and navigation, and efficient and

adaptive mowing patterns.

4. Create a mobile app for remote control and monitoring, enhancing usability for elderly

users and caregivers.

5. Evaluate the economic feasibility and scalability of the system for broader consumer

adoption.

By combining renewable energy with cutting-edge AI-driven navigation, this project

seeks to move beyond the limitations of existing robotic mowers. At the same time, it focuses on

user accessibility, particularly for elderly individuals.

Adopted Approach

The adopted approach integrates multiple technological domains into a cohesive system.

The mower’s driving function will run on a compact onboard computer, using an STM32N6

microcontroller from STMicroelectronics. The MCU comes with a built-in proprietary Neural

Accelerator, the first of its kind from STM, which can operate at 600 GOPS, more than enough for our use case [15]. LiDAR sensors will generate real-time point clouds of the mowing

environment. When these are fused with visual detection, they will allow the system to

triangulate obstacles, calculate optimal paths, and maintain consistent mowing coverage. This

approach, called Simultaneous Localization And Mapping (SLAM), is not new; yet its pairing

with deep learning, and its deployment on an autonomous lawnmower will be fairly novel.

The solar charging system will be implemented through a mini-shed housing 3

monocrystalline photovoltaic panels. The mower will autonomously navigate to the shed when

battery levels are low or after completing a mowing cycle. This system not only minimizes

manual intervention but also ensures the mower remains functional in off-grid conditions.

For elderly accessibility, a mobile/web app will provide real-time monitoring, scheduling,

and manual override options. This app-based control will address usability concerns while giving

family members the ability to assist remotely. This measure will enhance accessibility for all

populations. This hybrid approach, combining AI-driven perception, LiDAR-based navigation,

solar sustainability, and human-centered design, distinguishes the SolarVision Mower from

existing robotic lawnmowers that typically adopt only one or two of these technologies.

Current Trends in the Field

The global market for robotic lawnmowers has expanded rapidly. It had a market size of

USD 1.5 billion in 2023 [16], and USD 1.15 billion in 2024 [17]. This was estimated to grow up

to USD 2 billion by 2030 [16], and USD 3.01 billion by 2032 [17]. The market has an estimated

Compound Annual Growth Rate (CAGR) of between 10.9% to 14.8% between 2023 and 2030

[10,16,17]. Much of this growth is driven by consumer demand for convenience and eco-friendly

outdoor equipment. Leading manufacturers such as Husqvarna, Bosch, and Worx are

incorporating GPS-based navigation and smartphone connectivity into their products [17].

However, the majority of these systems still rely on docking stations powered by conventional

electricity.

Figure 3: Global robotic lawn mower market trends [17].

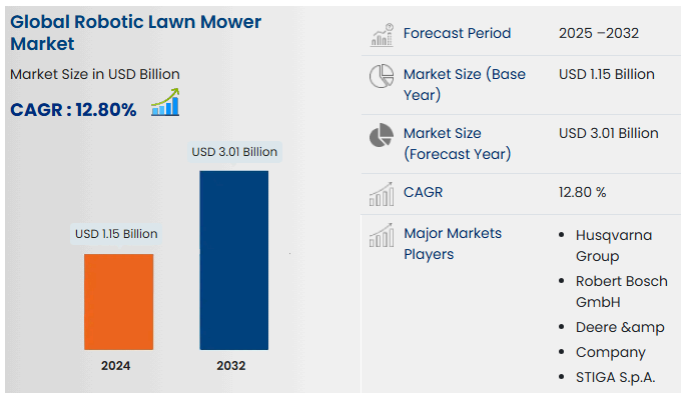
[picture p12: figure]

From a research perspective, there is growing emphasis on integrating autonomous

navigation technologies from self-driving vehicles into smaller consumer robotics. For instance,

researchers have explored LiDAR-GPS fusion for precision agriculture robots [11,12,18,19] and

deep learning for real-time obstacle avoidance in mobile robots [20]. The adoption of renewable

energy solutions, including solar integration, remains an emerging area, with limited deployment

in commercial robotic mowers despite demonstrated potential in academic prototypes [21].

Ethically, robotic mowers raise debates over safety, energy sustainability, and labor

displacement [13]. While autonomous mowing reduces physical strain for elderly users, and

more generally is convenient for everyone, improper deployment could lead to safety hazards.

Manufacturers are therefore under increasing pressure to meet ethical design standards,

emphasizing safety certifications, AI transparency, and energy efficiency.

Economically, as battery and solar technologies become cheaper, the cost of sustainable

robotic systems is expected to decline [22]. This trend could improve accessibility and democratize advanced lawn care technologies for broader populations. This will particularly

affect regions where manual mowing remains labor-intensive.

Related Real-World Commercial Systems

A review of current commercial systems reveals several benchmarks and limitations.

Husqvarna Automower remains a leading product, but it requires perimeter wire installation and

relies on traditional charging docks [2]. Bosch’s Indego line integrates GPS mapping but has

limited obstacle detection capabilities. The Worx Landroid offers smartphone connectivity and

scheduling features but, like others, is not solar-powered [23]. However, these existing

prototypes offer significant frameworks and highlight the niche on which the proposed mower

will be building.

Research prototypes, such as solar-powered agricultural robots for crop management,

have demonstrated the feasibility of renewable-powered autonomy [11,12,18,19]. However, the

direct application of solar energy in consumer lawnmowers is still underexplored. This gap

provides an opportunity for the SolarVision Mower to distinguish itself as one of the first to

integrate solar charging, deep learning based vision, and SLAM-based navigation into a unified

consumer-ready system.

From a sustainability perspective, our design directly addresses the ethical and economic

concerns surrounding energy use and affordability. The proposed mower leverages renewable

energy and reduces reliance on costly wired navigation. Therefore, it has potential for both

ecological and social impact. While current commercial systems have advanced beyond basic

wire-guided models, they remain constrained by energy dependence and limited perception.

Additionally, by adopting YOLO and LiDAR for object detection and navigation, our prototype

offers a forward-looking solution with the potential to reshape the consumer robotics landscape.

Members Responsibilities and Technical Goals

Each technical goal will be spread out through different time frames for completion.

Throughout those time frames, the group as a whole will put in a combined effort, where each

component under the major technical goal will be split up among the 4 of us. The major technical

goals will be tackled sequentially, starting with the Solar Shed, followed by the Battery

Management System for the on-board battery, the autonomous navigation system, and finally the

Android app to monitor and control the lawnmower through the phone if need be. Realizing

these goals in a timely manner is absolutely essential to the completion of this project, and as

such, a more detailed overview is given below.

Firstly, we will build the Solar Shed. The shed itself, which will be built out of wood, will

be made waterproof, and covered in 3 series 12V 100W peak output Monocrystalline solar

panels. These solar panels will then charge a stationary deep cycle Lead Acid battery pack

through a custom Battery Management System (BMS), which will then charge the mower’s

Lithium Ion 36V 10Ah battery through a second BMS. The Solar Shed will operate as a

complete unit in-and-of itself, not attached to the grid’s power system. While this does have its

drawbacks, such as being unable to charge on cloudy days, we believe that it will bring around a

simplicity of installation that won’t be garnered by connecting the system to the grid.

Additionally, since mowers are typically used infrequently (once every two or three weeks), the

300W output should be more than enough to maintain the mower’s state-of-charge.

Next, we will start working on the autonomous mower itself. Or rather, a bench-tested

version of it. At this point in time, all the 4 of us will tackle separate tasks within the umbrella of

this bench-test; namely, the LiDAR system, the GPS/RTK system, the YOLO vision based object detection system, and the Sound-based Triangulation system. Each of us will prepare our sensors

and their corresponding interfaces, such that when the time to put the pieces together comes

around, the sensor system will be sufficiently abstracted away, to the point that we only need to

worry about the actual navigation algorithm and final physical design of the mower.

Next, we will split up into groups of 2. One group will be working on the navigation

system for the mower, and the other will work on the physical design, and as such, will hold each

other accountable to meet our deadlines. As stated earlier, our main design constraints for both

the navigation system and the physical design of the mower, is cheapness and reliability. For

instance, a turning mechanism for the wheels may prove challenging; rather a 4-wheel drive

design with Mecanum wheels may be more cost-effective and reliable, and also provide the

benefits of a shorter turning radius [28]. We also plan to build a custom Lithium Ion battery out

of 18650 cells in a 10S4P configuration, as this approach drastically reduces the cost compared

to buying a ready-made battery pack. Once the body of the mower and the navigation system is

complete, we will attempt to create an Android app to control/override the mower remotely, if

we have the time.

Below is a bullet point list of how we anticipate our project will pan out. We will be

starting it soon this semester, and aim to complete it by the end of next semester.

1. Autonomous Driving (Ideas - not necessarily using them all)
a. LiDAR
i. Interface with Arduino
b. GPS/RTK
i. Interface with Arduino
c. YOLO
i. Interface Arduino with Computer running YOLO ii. Run Navigation System on Computer
d. Triangulation System - TBD
2. Software App
a. Connection with Arduino - Bluetooth/WiFi b. Controls/Overrides Mower if needed
3. Overall Design
a. Cost Efficient
i. Main idea - Make it Cheaper and Better than Market!
b. Lawnmower Design
i. Wheel Design Where It Can Drive Vertically and Horizontally
1. Mecanum wheels.
ii. | Water and Heat Resistance
iii. | Servo Motor Actuated Mower Height
1. Arduino Based; App Connected
c. Shed Design
i. 100W Monocrystalline Solar Panel ii. Batteries
1. Lead Acid fixed battery pack, Lithium Ion on-board battery pack
2. BMS
a. Boost Converter and Regulator for the Fixed Lead Acid
| battery pack (12V → 48V)
b. Charging System to Charge the Mower
c. BMS for the On-Board Battery itself
iii. Lightweight

Projected Community Impact and Relevant Ethical Issues

The proposed project will have significant benefits for the community. First, it will be a

resource for the elderly and people living with disabilities. These community members often

struggle to do yardwork, and sometimes they can not do it because it requires considerable

physical effort [24]. Because of its automation features, the lawnmower will improve the quality

of life, promote independence, and reduce the cost of lawn care.

Besides, the lawnmower will protect the environment from fossil fuel damage as it relies

on solar power. Lawnmowers that are powered by gas pollute the environment through carbon

dioxide and particulate matter emissions [25]. Solar energy and efficient batteries for power

storage ensure that this project lowers the carbon footprint and promotes sustainability [6,7,8].

Automated mowing also ensures that lawns stay healthy at all times, supporting the sequestration

of carbon and biodiversity [11].

Additionally, the automated lawnmower makes resource management easier. The system

utilizes LiDAR-based navigation and YOLO object detection techniques. These ensure it avoids

unnecessary mowing, prevents collisions, and reduces energy waste. [3,4,15]. The proposed

mower, therefore, aligns itself with the current and future trends in farming and landscaping,

which are both innovative and sustainable.

Despite the benefits highlighted above, the YOLO lawnmower project raises some ethical

issues that must be addressed. The first issue is safety around residential areas. Automated

machines can harm children, pets, or local wildlife [13,26]. Therefore, they must be adequately

engineered with safety measures. For the proposed project, thorough testing and the use of

fail-safe systems will help improve safety. In addition to safety, automated mowers also pose the

risk of displacing human labor [27]. The likelihood of causing job loss could lead to project

resistance. Therefore, educating community members on the benefits of the automated mowers

will be necessary.

This project seeks to balance technological advancement and social responsibility. It

prioritizes safety, accessibility, and sustainability at its core. This way, community members will

reap maximum benefits while the project avoids ethical risks.

Relevant Engineering Standards, Project Constraints, Risk, and Uncertainty

### 1.1 Engineering Standards

A. IEEE 1547-2018: Standard for Interconnection and Interoperability of Distributed

Energy Resources with Associated Electric Power Systems Interfaces a. IEEE 1547 establishes criteria for integrating distributed renewable energy

systems, such as photovoltaic (PV) units, into existing grids. Although the

SolarVision Mower functions as an off-grid system, this standard is relevant for

its solar charging module. This ensures proper design of the charge controller,

inverter, and safety cutoff mechanisms [29]. Following these guidelines promotes

energy efficiency and safe operation under variable sunlight conditions.

B. IEEE 1028-2008: Standard for Software Reviews and Audits
a. Because the mower’s autonomous functions rely heavily on YOLO-based object

detection and LIDAR sensor fusion, the software quality directly affects safety

and reliability. IEEE 1028 provides procedures for systematic software

verification, design reviews, and audits [30]. Implementing this standard ensures

that code modules related to image recognition, sensor fusion, and control logic

undergo formal inspection and testing. This reduces the likelihood of undetected

software bugs or faulty decision-making algorithms.

C. IEEE 61508-2010 / IEC 61508: Functional Safety of

Electrical/Electronic/Programmable Electronic Safety-Related Systems

a. This is a foundational international standard that governs functional safety in

autonomous and robotic systems. It defines requirements for system reliability,

hardware redundancy, and response to hazardous situations [31]. For the

SolarVision Mower, compliance means integrating fail-safe mechanisms. These

include emergency stop sensors, automatic power cut-off when detecting human

presence, and obstacle avoidance algorithms validated under safety integrity levels (SILs). Using functional safety guidelines ensures the robot minimizes the

probability of injury or property damage in unpredictable outdoor environments.

D. IEEE 802.11: Standard for Wireless LAN Communication
a. Because the mower can be remotely controlled and monitored through a mobile

application, reliable wireless communication is critical. IEEE 802.11 provides

protocols for Wi-Fi communication, ensuring secure and interference-resistant

data transmission [32]. Adhering to this standard supports smooth user-device

interaction. It will boost remote start/stop commands, diagnostic data upload, and

firmware updates.

E. ISO 8373:2021: Robotics – Vocabulary
a. This ISO standard defines terminology and basic concepts used in robotics [33].

Although the standard was withdrawn, it is essential for establishing a shared

understanding within the design team and aligning with research literature. By

classifying the mower as a “mobile service robot,” the team can apply appropriate

risk assessment and operational design standards as recommended by ISO.

### 1.2 Major Categories of Project Constraints

(a) Technical Constraints

The SolarVision Mower integrates multiple advanced technologies, each with its own

limitations. The accuracy of object detection is restricted by lighting conditions and the

processing power of the embedded computing system. For example, the YOLOv5 model

performs best under stable illumination; shadows or reflective surfaces can lead to false

detections [15]. Additionally, LIDAR sensors may exhibit reduced precision in heavy rain or when the laser signal is scattered by tall grass [4]. Thus, our project will include simple weather

detection, to find the best times to mow a lawn.

The battery capacity also imposes a significant technical limit. To sustain mowing operations and

sensor processing, the power management system must efficiently battery storage, and energy

consumption. Furthermore, autonomous navigation requires a real-time operating system (RTOS)

capable of handling multiple data streams simultaneously without lag [34]. Any

hardware-software mismatch could cause delays that affect path accuracy and obstacle

avoidance. Thus, for safety reasons, our mower will utilize normally open relays/switches

between the power supply and all major loads (motors). This will ensure that upon loss of power,

or a software triggered signal, the motors can be forced to shut off.

Lastly, safety redundancy is technically demanding. The mower must incorporate multiple

sensors (infrared, ultrasonic, and mechanical bumpers) to ensure that even if one fails, others still

provide fail-safe feedback. Implementing these redundancies increases complexity, testing time,

and cost. However, it is necessary for compliance with IEC 61508 safety standards [31].

(b) Economic (Budget) Constraints

Budget constraints are particularly relevant for a prototype project built using student or

institutional funding. High-quality LIDAR sensors (such as Velodyne or Ouster) and NVIDIA

Jetson-class processors can significantly increase costs. A single industrial-grade sensor can

exceed USD 1,000. Reliable lithium-ion battery packs and photovoltaic modules further increase

expenses [28].

To remain cost-effective, the design uses open-source machine learning frameworks and

affordable hardware alternatives such as RPLIDAR for distance sensing and the novel STM32N6

(currently $20 on Mouser Electronics) for vision inference. Even then, balancing performance

versus cost remains a challenge. Low-cost components may have limited durability or lower

precision.

Economic sustainability is also tied to manufacturing scalability. While the prototype may

operate reliably, commercial production would demand cost optimization in materials, mass

manufacturing, and supply chain logistics [35]. Thus, cost-benefit analysis must continue beyond

the prototype phase to determine whether the mower can compete with existing models.

(c) Environmental and Sustainability Constraints

The environmental motivation behind this project is strong. It aims at reducing emissions from

gas-powered lawnmowers and supporting sustainable home automation. According to the U.S.

Environmental Protection Agency (EPA), small gas engines produce a disproportionate share of

lawn care emissions. This contributes to carbon monoxide and volatile organic compounds [36].

The SolarVision Mower eliminates fossil fuel dependence through solar recharging and

low-voltage DC operation, directly reducing the carbon footprint.

However, environmental constraints also involve energy storage, material choice, and disposal.

Lithium-ion batteries, while efficient, pose recycling challenges and potential fire hazards if

mishandled. To comply with sustainability guidelines, the design emphasizes modularity,

allowing batteries to be replaced or recycled independently. Solar panels must also meet

durability and efficiency standards under outdoor exposure.

Weather variability presents an inherent environmental limitation. The mower’s solar charging

rate depends on sunlight availability, meaning overcast conditions may require the system to

postpone mowing or limit its operational window. The autonomous scheduling algorithm must

therefore integrate weather forecasts to optimize mowing intervals.

### 1.3 Risk and Uncertainty Assessment

### Risk Table

Technical Goals | Risk Level
Low | Moderate | High
Object Detection (YOLO) | | The model misclassifies obstacles in poor lighting or tall grass. Mitigation: Train model with diverse, perhaps custom datasets; integrate LIDAR depth confirmation.
Sensor Fusion | | | LIDAR and camera data desynchronization. Mitigation: Implement timestamp synchronization and real-time data buffering.

Battery Management | | Overcharging, overheating, or premature degradation. Mitigation: Add temperature sensors and overcurrent protection circuitry.
Solar Charging Dock | Inefficient charging during cloudy weather. Mitigation: Include backup plug-in charging option and energy storage estimation algorithm.
Software Reliability | | Unexpected crash or algorithm loop due to memory overload. Mitigation: Follow IEEE 1028 reviews and continuous integration testing.
Mechanical Design | | Blade collision or motor failure under uneven terrain. Mitigation: Add automatic shutdown sensors and reinforced housing.
Network Communication | Wi-Fi connectivity failure causing loss of remote control. Mitigation: Integrate fallback manual override and local control mode.

Environmental Impact | Battery disposal or PV panel waste. Mitigation: Use recyclable materials and certified disposal vendors.
Legal / Safety Compliance | | Injury or property damage during autonomous operation. Mitigation: Comply with IEC 61508 functional safety protocols and emergency stop design.
Economic Feasibility | Prototype costs exceed projected budget. Mitigation: Utilize low-cost open-source components and staged development milestones.

Discussion of Risks and Mitigation

I. Technical Risks
A. The most critical risks arise from sensor reliability and navigation accuracy.

Because the mower relies on visual data, conditions like dusk, rain, or dense

foliage can impair YOLO’s accuracy. To mitigate this, multi-sensor fusion will be

employed, combining visual recognition with depth sensing to ensure redundancy

[37]. The risk remains moderate, as environmental testing may reveal new edge

cases.

II. Economic Risks

A. The project’s funding limits influence hardware selection. A low-budget prototype
| may underperform compared to commercial models. This will potentially lead to
| underestimation of cost-to-performance ratios. To control this, the design follows
| an incremental approach. First, we will develop a proof of concept before scaling.
| Additionally, using modular parts allows easy replacement without rebuilding the
| entire system.
III. | Safety and Legal Risks:
A. Autonomous mowing poses serious safety concerns, especially in public or
| residential areas. The risk level is high if fail-safe mechanisms are not rigorously
| tested. To meet functional safety standards (IEC 61508), the mower will feature
| multiple safety layers [31]. These include proximity sensors, AI-based human
| detection, and an emergency stop button accessible both physically and via the
| mobile app.
IV. | Environmental Risks
A. While solar power reduces emissions, weather dependency introduces operational
| uncertainty. Extended cloudy days may delay mowing schedules, creating user
| dissatisfaction. This is mitigated through adaptive scheduling, where the system
| monitors battery charge and predicts available solar energy. Additionally,
| recyclable components and minimal use of plastics reduce environmental
| footprint.
V. Manufacturing and Sustainability Risks

A. Transitioning from prototype to large-scale production introduces uncertainty in

cost and durability. Early design documentation and compliance with IEEE/IEC

standards will ease this transition by providing traceable validation steps.

Sustainable design choices align the mower with circular economy principles.

### 1.4 Uncertainty Factors and Future Considerations

Uncertainty in this project stems from technological evolution and external environmental

factors. Advances in AI vision algorithms, for instance, may soon make the YOLO model

obsolete or less efficient compared to emerging transformer-based architectures. Thus, the

system is designed with software modularity to allow for future upgrades without hardware

replacement.

Another uncertainty lies in solar energy availability, which is variable across seasons and

geographical regions. Long-term performance assessment under different latitudes and climates

will be necessary to validate system reliability. Similarly, the long-term degradation of

photovoltaic panels and batteries introduces operational unpredictability that can only be

measured through field testing over several months.

Legal and ethical uncertainties also exist. The mower must comply with local regulations

concerning autonomous machinery in residential areas. For instance, some municipalities require

geofencing to prevent robotic devices from crossing property boundaries. Public perception and

acceptance may further influence adoption rates, particularly concerning safety and job displacement fears in the landscaping sector [28]. Despite these uncertainties, the SolarVision

Mower remains a promising contribution to sustainable automation.

Design methodology, prototyping, validation, and hardware block diagram

For the purposes of this project, we created a diagram (and approximate timeline) of how

we expect this project to flow. As mentioned in the Technical Goals section, we aim to tackle

large portions of the project as a group, and then subdivide said portions between us. As such, we

will begin (starting in November) to build a Solar Shed, which will house the completed mower.

Our hope is that the bench testing, prototyping, and design iterations of the mower itself

will take much more time than designing the Solar Shed. As such, we’ve decided to begin bench

testing the components of the project by this December at the latest. This bench test entails the

following:

- Individually testing each sensor/motor component that will be used (LiDAR, GPS/RTK,

YOLO, drive motors, and the height adjustment motor).

- Creating a modular software interface that will ultimately allow us to abstract the

hardware away by the time we get to the next phase: Autonomous Navigation.

Once the bench testing and interfacing is complete, we will transition to the Autonomous

Navigation phase of our project. In this phase, we will begin the software development for the

navigation of the mower. This entails the following:

- Utilizing the previously established interfaces to effectively communicate with the

hardware components.

- Writing software to locate the mower in 3d space, map out the given lawn, and run an

optimal path algorithm to mow the entire lawn with the least distance travelled.

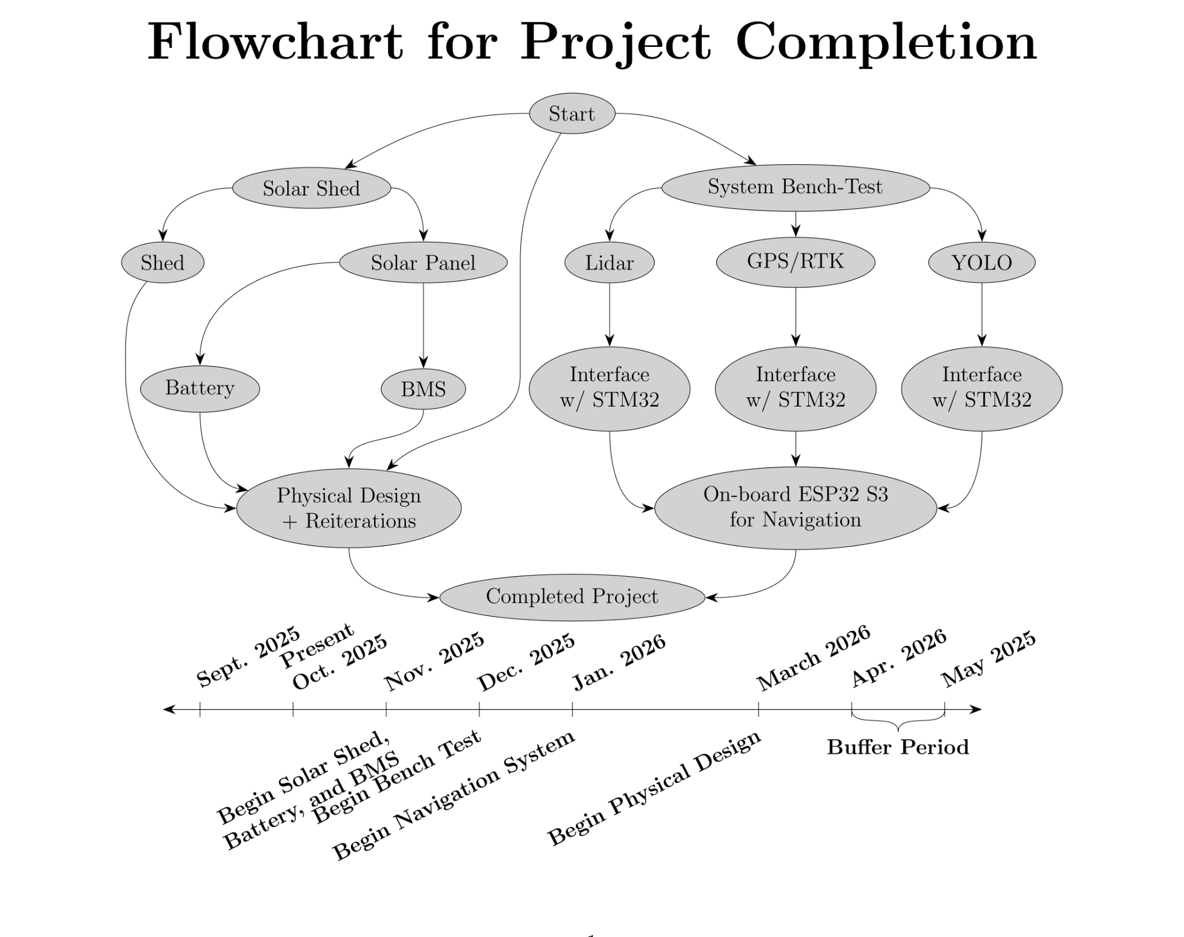
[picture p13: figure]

For the hardware side of our project, we’ve decided to use the following components:

- Sensors:
- Lidar: Adafruit-Slamtec RPLIDAR A1
- Camera: Standard USB Logitech Camera
- GPS: Adafruit 66 channel GPS Module
- Blade speed sensor: Custom built with Infrared Sensor
- On-board STM32N6 SBC
- Motors:

- Blade Motor: 200W DC Motor
- Mower Height Motor: Standard 12V Linear Actuator
- Left and Right Motors: Geared 12V 250W Motors
- Battery Module
- Custom built 36V 10Ah 18650 battery pack
- 10S4P Battery Management System
- Inference Engine and System Controller:
- Inference: STM32N6 SBC, with C++ YOLO inference engine, utilizing NPU
- System Controller: ESP32 S3, for SLAM object detection and pathfinding.

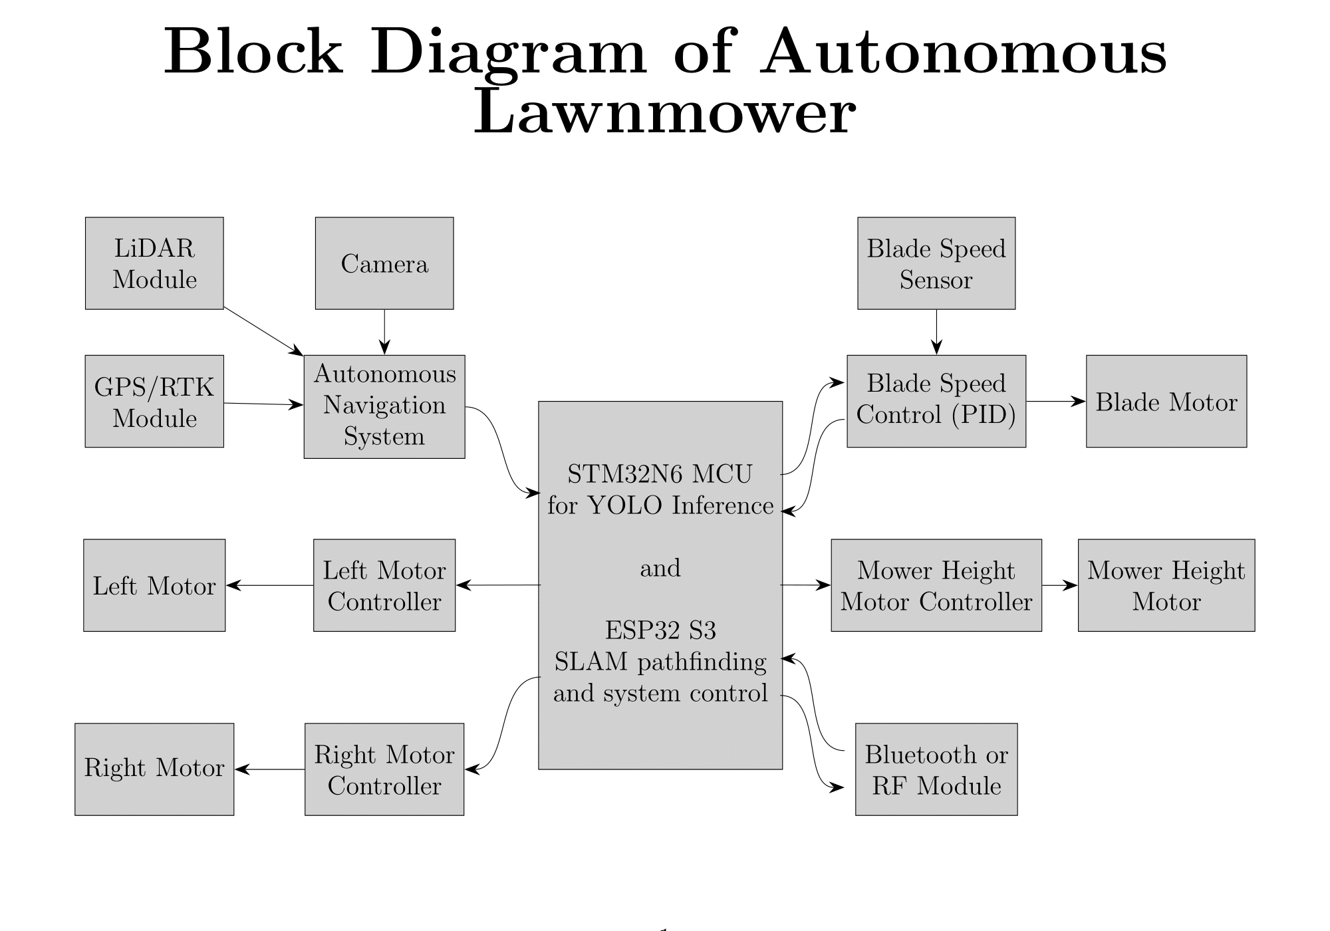
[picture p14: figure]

Relevant Technical Background Selected Technical Articles

Article 1: The YOLO Framework: A Comprehensive Review of Evolution, Applications,

and Benchmarks in Object Detection

Authors: M. L. Ali and Z. Zhang

Journal: Computers, vol. 13, no. 12, p. 336, 2024.

DOI: 10.3390/computers13120336

Link: https://doi.org/10.3390/computers13120336

ISBN: ISSN 2073-431X

Here, the review paper will compare the evolution of the YOLO (You Only Look Once)

model between YOLOv1 and YOLOv8, as well as the architectural upgrades that enable

real-time object detection on embedded and edge devices. The article highlights YOLOv5 and

YOLOv7 as applicable in autonomous mobile systems that require low-latency inference, such

as robotics and intelligent surveillance. It also demonstrates the performance on the benchmarks

of COCO and Pascal datasets, which confirms the accuracy-speed tradeoff of YOLO when

compared to R-CNN and SSD approaches [38].

Relevance and Comparison

The SolarVision Mower advertisement utilizes YOLOv5 as its primary object detection

model for categorizing real-time obstacles in real-time. Unlike the general-purpose applications,

the architecture of YOLO in this project is tailored to the requirements of an outdoor

environment, where LiDAR point clouds and the computational constraints of solar power are

present [38]. It is new, as it utilizes visual detection with LiDAR-based spatial awareness to

autonomously mow the lawn in a design that has not previously been optimized for outdoor

renewable-powered robotics.

Article 2: LiDAR Technology for UAV Detection: From Fundamentals and Operational

Principles to Advanced Detection and Classification Techniques

Authors: U. Seidaliyeva, L. Ilipbayeva, D. Utebayeva et al.

Journal: Sensors, vol. 25, no. 9, p. 2757, 2025.

DOI: 10.3390/s25092757

Link: https://doi.org/10.3390/s25092757

ISBN: ISSN 1424-8220

The principles of LiDAR systems, which the authors will discuss in this paper, include

distance measurement based on the time-of-flight principle, angular resolution, and object

classification. It illustrates that LiDAR is applicable in 3D mapping and tracking motion,

especially with UAVs that require adequate environmental modeling [39]. The scientific

literature review discusses scanning, point cloud filters, sensor fusion, and computer vision

models. This is designed to enhance scanning in various lighting conditions and weather.

Relevance and Comparison

The SolarVision Mower follows the same principle as LiDAR, aiming to work efficiently

in diverse ground conditions through the use of technology. The LiDAR to be utilized in this

project is modified to scan the surrounding environment and dynamically avoid objects in a

residential area. The LiDAR and YOLO-based system also consumes less energy, and it is less

sensitive to weather, which is attributed to its solar power usage and low-power processors. This

is because it has been able to operate with reduced discretion and, consequently, can work on a

smaller scale [39].

Article 3: Transforming Edge AI: The power of neural processing units in modern

microcontrollers

Authors: White paper from STMicroelectronics

Link:https://content.st.com/whitepaper-transforming-edge-ai-with-npus-in-microcontrollers-z11-

5780.html (https://content.st.com/whitepaper-transforming-edge-ai-with-npus-in-microcontrollers-z11-5780.html)

AI/ML has come a long way in the last few decades, and as of late, deep learning on the

edge has grown substantially. Traditional general purpose processors are capable of running

these advanced models, but not at any scale needed to meet demand. The authors of this

whitepaper thus introduced STM’s proprietary Neural-ART Accelerator, capable of increasing

inference speed up to 127x when compared to CPU-only ARM Cortex-M55s (when running

INT8 quantized and pruned Tiny YOLOv2). This enables, for the first time, inexpensive object

detection at up to 32 fps, running on a fraction of a watt.

Relevance and Comparison

This directly relates to the SolarVision Mower, as it will contain an STM32N6 at its core,

running a YOLOv8n model directly on the MCU’s Neural Accelerator. This design dramatically

improves the safety and reliability of the mower, as a higher throughput at the image processor

directly correlates with a higher accuracy during path planning and object detection.

### 8.2 Selected Patents

Patent 1: Autonomous Lawn Mower and Method for Operating the Same

Patent No.: US 11,215,987 B2

Inventors: J. Wahl, H. Björkman, and L. Eriksson

Assignee: Husqvarna AB

Publication Date: Jan. 4, 2022

Abstract and Description

This patent describes a robotic lawnmower equipped with perimeter wire navigation and

a collision sensor. The mower will be guided along a fixed, predetermined route and will charge

its batteries at a grid-based charging point. Though location-bound and without computer vision,

it is efficient [40].

Comparison

The SolarVision Mower utilizes LiDAR-based mapping and YOLO-based visual

perception, eliminating the need for wired boundary navigation.

Patent 2: Solar-Powered Automated Grass Cutting Robot

Patent No.: US 10,941,872 B2

Inventors: K. Takahashi and Y. Fukuda

Assignee: Honda Motor Co., Ltd.

Publication Date: Mar. 9, 2021

Abstract and Description

A photovoltaic-powered robot mower charges a lithium battery during operation. Its

navigation utilizes infrared and proximity sensors to avoid obstacles [41]. Although the patent

can unite renewable energy and automation, it lacks a machine-learning-based perception that

limits the distinction of obstacles and adaptive path planning.

Comparison

The SolarVision Mower is even broader as it merges solar energy with the integration of

YOLOv5 and LiDAR to conduct intelligent classification and environmentally responsible

navigation. The ability of a mobile application to monitor and modify the schedule also enhances

the ease and complexity of the automation for customers.

Patent 3: LiDAR-Based Collision Avoidance for Autonomous Ground Vehicles

Patent No.: US 11,764,001 B1

Inventors: B. Yang, H. Kim, and S. Huang

Assignee: Boston Dynamics Inc.

Publication Date: Sep. 12, 2023

Abstract and Description

This patent introduces a LiDAR-based collision-avoidance system that applies to

real-time mapping on a 3D map and predictive motion estimation to prevent collisions with

obstacles. The technology is primarily intended for use in industrial/defense robots [42]. It is

involved with autonomous navigation under the dynamically changing conditions, multi-sensor

integration, and spatial segmentation.

Comparison

In the SolarVision Mower advertisement, the same LiDAR-associated safety concepts are

applied, but scaled down to the realm of home automation. Precision and energy efficiency are

also balanced in the mower, compared to small-scale, solar-limited operations, which focus on

high-speed land traversal [42]. The originality of the project lies in the integration of

LiDAR-YOLO fusion within the scope of renewable energy, and the design has also been

adjusted to support the needs of affordability and safety in the consumer environment.

### 8.3 Technical Summary and Synthesis

The technological basis of the SolarVision Mower design comprises all the literature

reviewed and patents. The scientific community confirms that deep learning (YOLO) and

LiDAR systems are already advanced enough to incorporate robots at a low price [39]. Until that

day, the existing patents [40,41,42] indicate that commercial mowers remain dependent on grid charging, wired boundaries, and simplistic sensors. SolarVision Mower has a distinctive feature

of a combination of three innovations:

i. Solar independence: complete charge of solar, independent of the grid.
ii. | Hybrid perception: The LiDAR depth image and YOLO real-time object detection are
| used to classify the obstacles.
iii. | Edge intelligence: real-time decision making using low-power computing based on the
| Raspberry Pi or Jetson Nano.
| Together, the innovations address the key weaknesses of the current commercial and

patented products: the lack of sustainability, the inadequate perception, and barriers to entry. The

SolarVision Mower is therefore not just a plus in the technical and ethical aspects (it is safer, has

a smaller carbon footprint, and makes older people more independent with intelligent, renewable,

and affordable automation), but also an advantage to the beneficiaries of the product themselves.

| Marketability and Lifecycle SolarVision Mower has high market potential as there is an increased trend of consumers

moving towards outdoor technologies that are sustainable and autonomous. It is estimated that by

2030, the global robotic lawn mower market would reach USD 4 billion and its compound

annual growth rate (CAGR) would be around 10-14 percent as more owners of houses purchase

innovative and environmentally friendly solutions [32]. The combination of renewable energy

and IoT technologies supports this tendency in the market, as systems of automated processes

supported by solar energy have significantly increased their popularity in response to the

increased energy cost and growing awareness of environmental issues.

| The SolarVision Mower is the only mower with a solar source of power as its primary

energy source, and it does not depend much on the electrical system, which reduces the operational costs. The rival products (Husqvarna Automower and Bosch Indego) are charged on

a battery with household electricity. In comparison, the photovoltaic-based charger and a

modular structure of SolarVision enhance cost-efficiency, lower the lifecycle emissions, and

attract sustainability-conscious communities and homeowners [30].

Economically, a cost of USD 400-600 per unit (estimated production cost of SolarVision)

is reached by utilizing inexpensive and open-source components (e.g., Raspberry Pi, LiDAR, and

solar PV modules), which allow the company to sell at USD 1,000-1,200. This is being

competitive in the high-end home automation market, besides encouraging environmental

accountability. The intended audience consists of the middle- and high-income families and

communities, retirees, and intelligent housing developers with a focus on sustainable planning

[29].

According to a lifecycle assessment (LCA) framework, the SolarVision Mower is based

on the principles of the circular economy, in which the components are modular, recycled, and

easy to maintain. Solar panels, motors, and battery systems can be easily replaced by themselves,

which contributes to the increased life of the products, as well as reduces waste [31]. As per the

Pyramid of Production Systems model, the mower passes through the design phase, production

phase, usage phase, and recycling phase with a low environmental footprint. The estimated

product life cycle is 7-10 years, where a software update is to project the product lifespan further

[33].

Altogether, SolarVision is a profitable, sustainable, and socially responsible innovation. It

combines the principles of environmental stewardship and viable engineering design, which have

long-term advantages to consumers and the sustainability agenda across the world. The

SolarVision Mower combines energy efficiency, affordability, and environmental protection; it

has excellent potential for success in the business and the environment.

Timeline and Milestones
As indicated in the flowchart, the project begins in September- October 2025 with the

manufacture of Solar Sled, Solar Panel, Battery and BMS and the commencement of the System

Bench-Test of the LiDAR, GPS/RTK, YOLO and triangulation sensors. It transfers to the start of

the Navigation System in November, 2025, composed of Arduino interfaces and early brevity of

YOLO, LiDAR, and SLAM. This goes up to December 2025 that the navigation branches will

converge and feasibility study would be conducted and the onboard navigation computer fed

with validated information. The project begins the Physical design and iterations in January 2026

with the integration of the earlier created power and navigation subsystems into the emerging

mechanical structure. The design cycling goes on to February 2026, to March 2026, when all the

subsystems converge to the node of the Completed Project. Finally, the month of April-May

2026 will act as a buffer period where more debugging, testing, and re-work will be carried out

after which the fully integrated system will then be finalized.

Time Period | Flowchart-Derived Milestone
Sept–Oct 2025 | Begin Solar Sled, Solar Panel, Battery, BMS, and System Bench-Test
Nov 2025 | Begin Navigation System (LiDAR → Arduino, GPS/RTK → Arduino, YOLO path, Triangulation path)
Dec 2025 | Continue Navigation System; complete Test for Feasibility; feed results to On-board Computer
Jan 2026 | Begin Physical Design + Iterations
Feb 2026 | Continue Physical Design + Reiterations
March 2026 | Integrate subsystems toward Completed Project
April–May 2026 | Buffer Period (additional integration, testing, and adjustments)

Conclusion
SolarVision Mower is an innovative design of sustainable automation of residential

landscapes. The design also incorporates solar energy, YOLO-based perception, and LiDAR

navigation, making it focus on the sustainability, safety, and accessibility concerns mentioned in

the previous sections directly. The project achieves these objectives due to novelty in the use of

renewable energy sources, the use of AI-based precision, and the design to meet the needs of

elderly and disabled people.

It is anticipated to be a complete prototype that is able to reliably mow autonomously

with minimum human participation. The device has the potential of becoming a commercial in

the emerging market of environmentally friendly smart devices that can lower the energy bill and

further develop environmental objectives. SolarVision Mower is part of the larger

decarbonization efforts; it promotes the UN Sustainable Development Goals (SDGs) concerning

affordable clean energy and sustainable urban areas.

The research work of ECE 416 in the future will aim to run field testing, to develop the

YOLO-LiDAR fusion algorithm, and to enhance the mobile connection. The project schedule

makes the technical objectives as feasible as possible, and the continuous validation is in line

with the IEEE and IEC standards of safety. In the end analysis, the SolarVision Mower serves the

interests of homeowners, the environment, and the community, as it combines ethical

responsibility with technological excellence, thus making it a feasible and socially responsible

technology to live in the modern world.

Project Appendix

Necessary Components:

- Batteries and BMS:
- 40 Samsung 18650 batteries, for 36V 10Ah battery pack in 10S 4P configuration
- 3 12V 15Ah deep cycle lead acid batteries for stationary power storage at shed
- 15A Lithium Ion BMS
- Solar and Power (stationary):
- 3 12V 50-100W Solar panels, will decide depending on size constraints
- MPPT Solar Charge Controller
- Power (on-board):
- High-power relay array for safety, charging, and motor switching.
- Custom PCB for drive, blade, and height motor controllers (all DC motors)
- 36V to 12V buck converter for low power electronics
- Logic:
- ESP32 S3 Dev-board
- STM32N6x7xx soldered to custom PCB
- 16MB PSRAM chip with Flexible Memory Controller interface (necessary to store YOLO weights)
- 433MHz RF Module for communicating with charging dock/server. Technical Documents:
- Fusion360 Documentation https://help.autodesk.com/view/fusion360/ENU/
- We will be using Fusion360 to design all the physical components for this project. Required parts will then be either 3D printed out of TPU, or milled out of aluminum.
- KiCAD Documentation https://docs.kicad.org/
- All PCB/Circuit Design (and some simulation) will be done in KiCAD. We will all need to learn and use KiCAD, and the documentation will thus be very important.
- STM32N6x7xx Datasheet and Reference manual. https://www.st.com/resource/en/datasheet/stm32n657a0.pdfhttps://www.st.com/resource/en/reference_manual/rm0486-stm32n647657xx-armbased-3 2bit-mcus-stmicroelectronics.pdf (https://www.st.com/resource/en/reference_manual/rm0486-stm32n647657xx-armbased-32bit-mcus-stmicroelectronics.pdf)
- The datasheet and reference manual will be essential to the project’s PCB design; specifically for pin configurations and finding footprint dimensions.
- STM32 ARM Cortex-M55 Programming Manual. https://www.st.com/resource/en/programming_manual/pm0273-stm32-cortexm55-mcus-programming-manual-stmicroelectronics.pdf (https://www.st.com/resource/en/programming_manual/pm0273-stm32-cortexm55-mcus-programming-manual-stmicroelectronics.pdf)
- The programming manual for STM32’s ARM Cortex-M55 line of processors will be essential to programming the MCU once completed.
- ESP32 Datasheet https://documentation.espressif.com/esp32-s3_datasheet_en.pdf
- We will be using an ESP32 S3 for collecting data from sensors and the STM32’s YOLO model, controlling the motors, and running the core pathfinding algorithm.
- Miscellaneous other datasheets for the Solar Panels, BMS, MPPT charge controller, and power electronics
Software Tools:
- Git: We will be using Git as the version control system for our project. The main repository will house all the 3D models, KiCAD files, code, and documentation for the project.
- KiCAD: To design the mower’s custom PCB, and simulate various components, we will be using KiCAD. It will house the main ESP32 dev board via header pins and sockets, as well as the STM32 chip directly on the PCB.
- Fusion360: We will use Fusion360 to design all the physical components of the mower. Namely:
- The mower’s body, which will be welded out of 2x2 carbon steel tubing, and attached to the chassis of an existing mower
- The mower’s attachments for motors, sensors, and other peripherals. Prototypes for these attachments will be 3D printed out of PLA, and the final versions will be out of TPU with significant infill, for strength.
- The mower’s electronics housing box, which will house the main controller’s PCB, the power electronics (relays, BMS, etc), as well as external LEDs as status indicators

Simulations:

- KiCAD: For hardware level simulations, such as passive/active circuits, amplifiers, voltage regulators, etc.
- QEMU: For low-level hardware emulation:
- Espressif’s fork of QEMU for the ESP32 to emulate code
- QEMU’s ARM Cortex-M55 emulator for STM32N6 emulations (not counting the neural accelerator)
Project Management Software:
- Git: We will use Git as the primary version control and project management software.

Bibliography

[1].Power Plant & Hire, “A Brief History of Robotic Mowers,” Power Plant & Hire, Oct. 7,

2023. [Online]. Available:

https://www.powerplant.ie/news/a-brief-history-of-robotic-mowers/. [Accessed: Sep. 23,

2025].

[2].Husqvarna, “How do Automower® Robotic Lawn Mowers work?” Husqvarna AB, 2025.

[Online]. Available:

https://www.husqvarna.com/us/discover/robotic-mowers/automower-how-it-works/.

[Accessed: Sep. 24, 2025].

[3].M. L. Ali and Z. Zhang, “The YOLO framework: A comprehensive review of evolution,

applications, and benchmarks in object detection,” Computers, vol. 13, no. 12, p. 336,

Dec. 14, 2024. doi: 10.3390/computers13120336.

[4].U. Seidaliyeva, L. Ilipbayeva, D. Utebayeva, N. Smailov, E. T. Matson, Y. Tashtay, M.

Turumbetov, and A. Sabibolda, “LiDAR Technology for UAV Detection: From

fundamentals and operational principles to advanced detection and classification

techniques,” Sensors, vol. 25, no. 9, p. 2757, 2025. doi: 10.3390/s25092757.

[5].K. Thilagavathi and V. Sanjana, “Autonomous Solar Powered Lawn Mower,” in Proc.

2023 2nd Int. Conf. Advancements in Electrical, Electronics, Communication, Computing

and Automation (ICAECA), Coimbatore, India, 2023, pp. 1–6. doi:

10.1109/ICAECA56562.2023.10200615.

[6].R. Mousavi, A. Mousavi, Y. Mousavi, M. Tavasoli, A. Arab, I. B. Kucukdemiral, A. Alfi,

and A. Fekih, “Revolutionizing solar energy resources: The central role of generative AI in elevating system sustainability and efficiency,” Applied Energy, vol. 382, p. 125296,

Mar. 15, 2025. doi: 10.1016/j.apenergy.2025.125296.

[7].M. Shahidehpour and M. Zhuang, “Achieving Energy Sustainability: Tackling Global

Challenges With Innovation, Equity, and Governance,” IEEE Energy Sustainability

Magazine, vol. 1, no. 1, pp. 12–31, May 2025. doi: 10.1109/ESM.2025.3559252.

[8].International Energy Agency, Renewables, 2025. [Online]. Available:

https://www.iea.org/energy-system/renewables. [Accessed: Sep. 25, 2025].

[9].Robot Lawn Mower, “Wire vs Wireless Robot Lawn Mower Which Is Better?” Jun. 3,

2025. [Online]. Available:

https://robotlawnmower.nz/blogs/batterypowered/wire-vs-wireless-robot-lawn-mower.

[Accessed: Sep. 23, 2025].

[10]. E. N. Selvanesan, K. W. Liew, C. H. Tay, J. A. Yeow, Y. J. Ng, P. L. Chong, and C. Q.

Kang, “A review of the performance of smart lawnmower development: theoretical and

practical implications,” Designs, vol. 9, no. 3, p. 55, May 2, 2025. doi:

10.3390/designs9030055.

[11]. M. Fontani, S. M. Luglio, L. Gagliardi, A. Peruzzi, C. Frasconi, M. Raffaelli, and M.

Fontanelli, “A Systematic Review of 59 Field Robots for Agricultural Tasks:

Applications, Trends, and Future Directions,” Agronomy, vol. 15, no. 9, p. 2185, Sep. 13,

2025. doi: 10.3390/agronomy15092185.

[12]. C. Q. Kang, P. K. Ng, and K. W. Liew, “A TRIZ-Integrated conceptual design process

of a smart lawnmower for uneven grassland,” Agronomy, vol. 12, no. 11, p. 2728, Nov. 3,

2022. doi: 10.3390/agronomy12112728.

[13]. S. L. Rasmussen, B. T. Schrøder, A. Berger, R. Sollmann, D. W. Macdonald, C.

Pertoldi, and A. K. Alstrup, “Testing the Impact of Robotic Lawn Mowers on European

Hedgehogs (Erinaceus europaeus) and Designing a Safety Test,” Animals, vol. 14, no. 1,

p. 122, Dec. 29, 2023. doi: 10.3390/ani14010122.

[14]. C. Wedel, “Two Years, Zero Regrets: My Robot Lawn Mower Is Still Worth Every

Penny,” CNET, Sep. 21, 2024. [Online]. Available:

https://www.cnet.com/home/yard-and-outdoors/two-years-zero-regrets-my-robot-lawn-m

ower-is-still-worth-every-penny/. (https://www.cnet.com/home/yard-and-outdoors/two-years-zero-regrets-my-robot-lawn-mower-is-still-worth-every-penny/) [Accessed: Sep. 24, 2025].

[15]. P. Amanatidis, D. Karampatzakis, G. Iosifidis, T. Lagkas, and A. Nikitas,

“Cooperative task execution for object detection in edge computing: An internet of things

application,” Applied Sciences, vol. 13, no. 8, p. 4982, Apr. 15, 2023. doi:

10.3390/app13084982.

[16]. Research and Markets, “Robotic Lawn Mowers Market Trends and Business

Strategies, Forecast to 2030,” Global Newswire, Dec. 11, 2024. [Online]. Available:

https://www.globenewswire.com/news-release/2024/12/11/2995233/28124/en/Robotic-L

awn-Mowers-Market-Trends-and-Business-Strategies-Forecast-to-2030.html. (https://www.globenewswire.com/news-release/2024/12/11/2995233/28124/en/Robotic-Lawn-Mowers-Market-Trends-and-Business-Strategies-Forecast-to-2030.html) [Accessed:

Sep. 23, 2025].

[17]. Data Bridge, “Global Robotic Lawn Mower Market Size, Share, and Trends Analysis

Report – Industry Overview and Forecast to 2032,” Data Bridge Market Research.

[Online]. Available:

https://www.databridgemarketresearch.com/reports/global-robotic-lawn-mower-market.

[Accessed: Sep. 25, 2025].

[18]. M. S. Hossain, M. Rahman, A. Rahman, M. M. Kabir, M. F. Mridha, J. Huang, and J.

Shin, “Automatic navigation and self-driving technology in agricultural machinery: A

state-of-the-art systematic review,” IEEE Access, vol. PP, no. 99, pp. 1–1, May 26, 2025.

doi: 10.1109/ACCESS.2025.3573324.

[19]. H. Wu, X. Wang, X. Chen, Y. Zhang, and Y. Zhang, “Review on Key Technologies

for Autonomous Navigation in Field Agricultural Machinery,” Agriculture, vol. 15, no.

12, p. 1297, Jun. 17, 2025. doi: 10.3390/agriculture15121297.

[20]. L. C. Sousa, Y. M. Silva, V. B. Schettino, T. M. Santos, A. R. Zachi, J. A. Gouvêa,

and M. F. Pinto, “Obstacle Avoidance Technique for Mobile Robots at Autonomous

Human-Robot Collaborative Warehouse Environments,” Sensors, vol. 25, no. 8, p. 2387,

Apr. 9, 2025. doi: 10.3390/s25082387.

[21]. A. Hassan, M. El Habrouk, and S. Deghedie, “Renewable Energy for Robots and

Robots for Renewable Energy–A Review,” Robotica, vol. 38, no. 9, pp. 1–29, 2020. doi:

10.1017/S0263574719001644.

[22]. I. Almusharraf, “Automation and its influence on sustainable development:

Economic, social, and environmental dimensions,” Sustainability, vol. 17, no. 4, p. 1754,

Feb. 19, 2025. doi: 10.3390/su17041754.

[23]. Robbans Blog, “Landroid vs Bosch Indego,” Jul. 19, 2021. [Online]. Available:

https://blog.robban.eu/2021/07/19/landroid-vs-bosch-indego.html. [Accessed: Sep. 24,

2025].

[24]. S. Jain, A. Khalore, and S. Patil, “Self-efficient and sustainable solar-powered robotic

lawn mower,” Int. J. Trend Res. Dev. (IJTRD), vol. 2, no. 6, Dec. 2015. [Online].

Available: https://www.ijtrd.com/papers/IJTRD1362.pdf.

[25]. S. B. Lerman and A. R. Contosta, “Lawn mowing frequency and its effects on

biogenic and anthropogenic carbon dioxide emissions,” Landscape Urban Plann., vol.

182, pp. 114–123, Feb. 2019, doi: 10.1016/j.landurbplan.2018.10.016.

[26]. UK Navimow, “Are Robot Lawn Mowers Safe Around Pets and Children?” UK

Navimow, 2025. [Online]. Available:

https://uknavimow.com/news/are-robot-lawn-mowers-safe-around-pets-and-children.

[Accessed: Sept. 30, 2025].

[27]. S. Ingle, “How could robotic mowers benefit landscaping pros?” Green Industry

Pros, Feb. 9, 2020. [Online]. Available:

https://www.greenindustrypros.com/industry-updates/article/21108699/how-could-roboti

c-mowers-benefit-landscaping-pros. (https://www.greenindustrypros.com/industry-updates/article/21108699/how-could-robotic-mowers-benefit-landscaping-pros) [Accessed: Sept. 30, 2025].

[28]. Zhewen Z, Hongliu Y, Chengjia W, Pu H, Jiangui W. “A comprehensive study on

Mecanum wheel-based mobility and suspension solutions for intelligent nursing

wheelchairs”. Sci Rep. 2024 Sep 4;14(1):20644. doi: 10.1038/s41598-024-71459-3.

PMID: 39232088; PMCID: PMC11375155.

[29]. Asim, Z., Shahzad, H. M. A., Ghodake, G., Mahmoud, K. A., Almomani, F., &

Rasool, K. (2025). Transforming agricultural food waste into bioplastics: Methods,

potential, and technological advances. Advanced Sustainable Systems, 9(3), 2400864.

https://doi.org/10.1002/adsu.202400864

[30]. Lu, T., & Halog, A. (2020). Towards better life cycle assessment and circular

economy: On recent studies on interrelationships among environmental sustainability,

food systems, and diet. International Journal of Sustainable Development & World

Ecology, 27(6), 515–523. https://doi.org/10.1080/13504509.2020.1734984

[31]. Mohanty, A. K., Wu, F., Mincheva, R., Hakkarainen, M., Raquez, J. M., Mielewski,

D. F., ... & Misra, M. (2022). Sustainable polymers. Nature Reviews Methods Primers,

2(1), 46. https://doi.org/10.1038/s43586-022-00124-8

[32]. Research and Markets. (2024). Global robotic lawn mower market forecast

2024–2030. https://www.researchandmarkets.com/reports/robotic-lawn-mower-market

[33]. Tartiu, V. E., Hurley, R., Baann, C., Briassoulis, D., Schettini, E., Convertino, F., ... &

Nizzetto, L. (2025). Addressing the environmental sustainability of plastics used in

agriculture: A multi-actor perspective. Cambridge Prisms: Plastics, 3, e5.

https://doi.org/10.1017/plc.2024.34

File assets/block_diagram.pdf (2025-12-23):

# Block Diagram of Autonomous Lawnmower

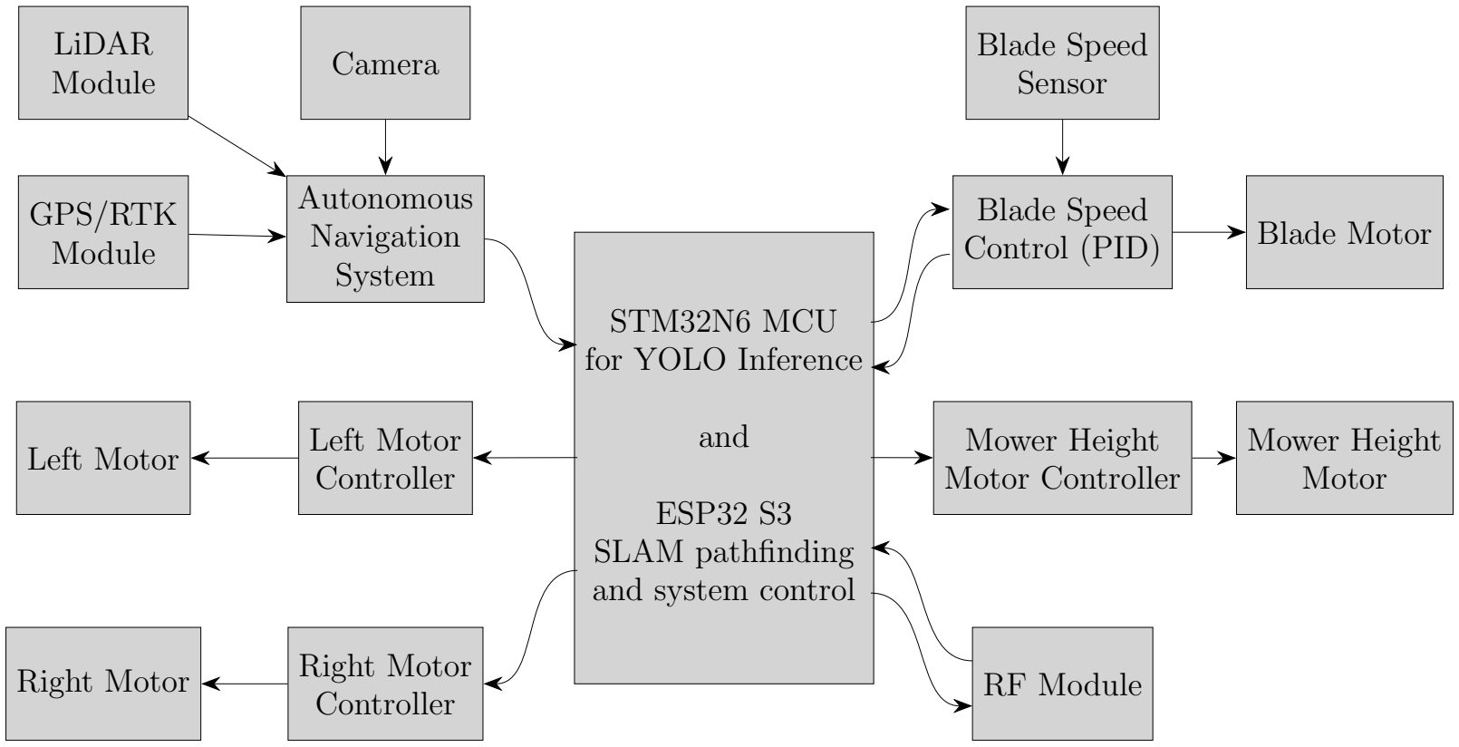
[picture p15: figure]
STM32N6 MCU for YOLO Inference; and; ESP32 S3 SLAM pathfinding and system control; Autonomous Navigation System; GPS/RTK Module; LiDAR; Module; Camera; Blade Speed Control (PID); Blade Speed Sensor; Blade Motor; Mower Height Motor Controller; Mower Height Motor; RF Module; Left Motor Controller Left Motor; Right Motor Controller Right Motor

1

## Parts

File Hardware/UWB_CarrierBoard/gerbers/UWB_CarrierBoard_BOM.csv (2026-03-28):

Designation | Designator | Footprint | Quantity | JLCPCB Part #
Conn_01x09_Socket | J2,J1 | PinSocket_1x09_P2.54mm_Vertical | 2 | C2897372
10k | R2,R3 | R_0402_1005Metric | 2 | C25531
D_TVS | D1 | SOT-723 | 1 | C233435
17k | R1 | R_0402_1005Metric | 1 | C25542
100u | C2 | C_0402_1005Metric | 1 | C88945
SPX5205-ADJ | U2 | SOT-23-5 | 1 | C6863

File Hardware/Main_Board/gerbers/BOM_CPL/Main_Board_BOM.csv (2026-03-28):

Id | Designator | Footprint | Quantity | Designation | Supplier and ref
1 | L1 | L_0805_2012Metric | 1 | 68u
2 | J5,J4 | PinSocket_1x08_P2.54mm_Vertical | 2 | Conn_01x08_Socket
3 | J2,J3 | PinSocket_1x22_P2.54mm_Vertical | 2 | Conn_01x22_Socket
4 | D1 | C_0805_2012Metric | 1 | D_Schottky
5 | J6 | PinSocket_1x05_P2.54mm_Vertical | 1 | Conn_01x05_Socket
6 | U2 | CONV_LM2596DSADJG | 1 | LM2596DSADJG
7 | J1 | TerminalBlock_bornier-2_P5.08mm | 1 | Conn_01x02_Socket
8 | C1 | CP_Radial_D4.0mm_P1.50mm | 1 | 220u
9 | U4 | STM32N6_Board | 1 | ~
10 | C2 | C_0805_2012Metric | 1 | 100u
11 | R2 | R_0603_1608Metric | 1 | 1k
12 | U1 | XCVR_ESP32-S3-DEVKITC-1U-N8R2 | 1 | ESP32-S3-DEVKITC-1U-N8R2
13 | U5 | SOT-23-5 | 1 | ~
14 | R4 | R_0603_1608Metric | 1 | 10k
15 | R1 | R_0603_1608Metric | 1 | 3k
16 | R3 | R_0603_1608Metric | 1 | 17k
17 | U3 | BU01 | 1 | DWM1000

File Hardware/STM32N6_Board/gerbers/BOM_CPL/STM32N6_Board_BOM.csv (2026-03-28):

Id | Designator | Footprint | Quantity | Designation | Supplier and ref
1 | R31 | R_0402_1005Metric | 1 | 200
2 | C42,C39,C41,C50,C40,C36 | C_0805_2012Metric_Pad1.18x1.45mm_HandSolder | 6 | 100u
3 | U8,U2,U4,U5,U3 | SOT-23-5 | 5 | SPX5205-ADJ
4 | C54,C53,C52,C49 | C_0402_1005Metric_Pad0.74x0.62mm_HandSolder | 4 | 12p
5 | D8,D10,D9,D7 | SOT-723 | 4 | D_TVS_Dual_AAC
6 | D4,D12 | LED_0805_2012Metric_Pad1.15x1.40mm_HandSolder | 2 | D_TVS
7 | R9,R27,R22 | R_0805_2012Metric_Pad1.20x1.40mm_HandSolder | 3 | 10k
8 | C56,C32,C22,C14,C33,C60,C13,C62,C48,C64,C30,C21,C16,C66,C34,C7,C31,C18,C68,C43,C8,C46,C15,C58,C19,C17 | C_0402_1005Metric | 26 | 100n
9 | C57,C1,C63,C47,C44,C45,C55,C59,C67,C65,C61 | C_0402_1005Metric | 11 | 4.7u
10 | R15,R29,R30,R28 | R_0402_1005Metric | 4 | 2k
11 | J10 | PinHeader_1x03_P2.54mm_Vertical | 1 | BOOT0
12 | R46,R49,R47,R48,R13,R45,R44 | R_0402_1005Metric | 7 | 0R
13 | R21,R3,R7,R5 | R_0805_2012Metric_Pad1.20x1.40mm_HandSolder | 4 | 15k
14 | FB2 | L_1206_3216Metric_Pad1.42x1.75mm_HandSolder | 1 | 70R@100M
15 | J12,J11 | PinSocket_1x18_P2.54mm_Vertical | 2 | Conn_01x18_Socket
16 | C4,C3,C5,C35 | C_0402_1005Metric | 4 | 15u
17 | R16,R26,R14,R17 | R_0402_1005Metric | 4 | 10k
18 | J9 | PinHeader_1x03_P2.54mm_Vertical | 1 | BOOT1
19 | U10 | SOT-23-5 | 1 | STMPS2151STR
20 | R8 | R_0805_2012Metric_Pad1.20x1.40mm_HandSolder | 1 | 17k
21 | J6 | PinHeader_1x05_P2.54mm_Vertical | 1 | Conn_01x05_Pin
22 | U14,U12,U9,U13 | ST_UQFN-6L_1.5x1.7mm_P0.5mm | 4 | ECMF2-40A100N6
23 | R4,R1,R6,R10 | R_0805_2012Metric_Pad1.20x1.40mm_HandSolder | 4 | 7k
24 | D2,D3 | LED_0603_1608Metric_Pad1.05x0.95mm_HandSolder | 2 | LED
25 | J1 | PinHeader_1x02_P2.54mm_Vertical | 1 | Conn_01x02_Pin
26 | C51 | C_0805_2012Metric_Pad1.18x1.45mm_HandSolder | 1 | 100n
27 | U11 | IS42S16800F-7BL_BGA54C80P9X9_800X800X120 | 1 | IS42S16800F-7BL
28 | R20 | R_0402_1005Metric | 1 | 20R
29 | D5 | LED_0805_2012Metric_Pad1.15x1.40mm_HandSolder | 1 | D
30 | J3 | PinHeader_1x08_P2.54mm_Vertical | 1 | Conn_01x08_Pin
31 | Y3 | 48MHz_Q22FA12800150_4Pin_2.0z1.6mm | 1 | 48MHz
32 | J7 | AMPHENOL_SFW15R-2STE1LF | 1 | SFW15R-2STE1LF
33 | U1 | STM32N657I0H3Q_VFBGA178_14x14 | 1 | STM32N657I0H3Q
34 | SW2 | SW_SPST_Omron_B3FS-101xP | 1 | SW_Push
35 | J13 | SHOUHAN_TYPE-C_16PIN_2MD__073_ | 1 | TYPE-C_16PIN_2MD__073_
36 | D6 | LED_0603_1608Metric_Pad1.05x0.95mm_HandSolder | 1 | LED_Small
37 | R18,R19,R23 | R_0402_1005Metric | 3 | 200R
38 | U7 | MX25LM51245GXD100_BGA24C100P5X5_600X800X120 | 1 | MX25LM51245GXDI00
39 | FB1 | L_1206_3216Metric_Pad1.42x1.75mm_HandSolder | 1 | 50R@100M
40 | R11 | R_0805_2012Metric_Pad1.20x1.40mm_HandSolder | 1 | 5k
41 | J5,J4 | PinHeader_1x18_P2.54mm_Vertical | 2 | Conn_01x18_Pin
42 | Y1 | 32kHz_SC-20S_2Pin_2.05x1.2mm | 1 | 32.768kHz
43 | C37 | C_0402_1005Metric | 1 | 470p
44 | C28,C26,C12,C25,C11,C23,C24,C27,C20 | C_0402_1005Metric | 9 | 1u
45 | C69,C29 | C_0805_2012Metric_Pad1.18x1.45mm_HandSolder | 2 | 1u
46 | L3 | L_1206_3216Metric_Pad1.42x1.75mm_HandSolder | 1 | 220u
47 | C38 | C_0402_1005Metric | 1 | 470u
48 | R25,R24 | R_0402_1005Metric | 2 | 5k
49 | L2 | L_1206_3216Metric_Pad1.42x1.75mm_HandSolder | 1 | 2.2n
50 | D1 | Schottky_DIOM4325X250N | 1 | D_Schottky
51 | C9,C10 | C_0402_1005Metric | 2 | 10u
52 | U6 | SO-8_3.9x4.9mm_P1.27mm | 1 | MC34064-ADJ-TR
53 | R12 | R_0805_2012Metric_Pad1.20x1.40mm_HandSolder | 1 | 3k

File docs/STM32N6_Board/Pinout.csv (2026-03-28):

Position | Name | Type | Signal | Label
A1 | PDR_ON | MonoIO
A2 | OTG2_HSDM | MonoIO
A3 | NC | NC
A4 | VDD33USB | Power
A5 | OTG1_HSDM | MonoIO | USB1_OTG_HS_DM
A6 | UCPD1_CC1 | MonoIO
A7 | PH1-OSC_OUT(PH1) | I/O
A8 | PC6 | I/O | HDP_HDP6
A9 | PC7 | I/O | TIM3_CH2
A10 | PE6 | I/O | I2C1_SDA
A11 | PD6 | I/O | FMC_A1
A12 | PD0 | I/O | FMC_A6
A13 | PD3 | I/O | FMC_A10
A14 | VSS | Power
B1 | PC14-OSC32_IN(OSC32_IN) | I/O
B2 | OTG2_HSDP | MonoIO
B3 | OTG1_ID | MonoIO | USB1_OTG_HS_ID
B4 | OTG2_TXRTUNE | MonoIO
B5 | OTG1_HSDP | MonoIO | USB1_OTG_HS_DP
B6 | UCPD1_CC2 | MonoIO
B7 | PH0-OSC_IN(PH0) | I/O
B8 | PC1 | I/O | UART4_TX
B9 | PE11 | I/O | FMC_SDNWE
B10 | PE15 | I/O | FMC_SDCKE0
B11 | PD7 | I/O | FMC_A2
B12 | PD1 | I/O | FMC_A7
B13 | PD4 | I/O | FMC_A11
B14 | PE9 | I/O | FMC_BA0
C1 | PC15-OSC32_OUT(OSC32_OUT) | I/O
C2 | VBAT | Power
C3 | PC13 | I/O | HDP_HDP5
C4 | NC | NC
C5 | OTG2_ID | MonoIO
C6 | PC8 | I/O | HDP_HDP0
C7 | PC11 | I/O | HDP_HDP3
C8 | PH9 | I/O | UART4_RX
C9 | PE14 | I/O | FMC_SDNE0
C10 | PE13 | I/O | FMC_SDNCAS
C11 | PD10 | I/O | FMC_A3
C12 | PD15 | I/O | FMC_A8
C13 | PE8 | I/O | USART3_TX
C14 | PE10 | I/O | FMC_BA1
D1 | V08CAP | Power
D2 | VFBSMPS | Power
D3 | BOOT0 | Boot
D4 | VDDA18USB | Power
D5 | OTG1_TXRTUNE | MonoIO
D6 | PC9 | I/O | HDP_HDP1
D7 | PC12 | I/O | HDP_HDP4
D8 | PC10 | I/O | HDP_HDP2
D9 | PE5 | I/O | I2C1_SCL
D10 | PE12 | I/O | FMC_SDNRAS
D11 | PE7 | I/O | FMC_A4
D12 | PD14 | I/O | FMC_A9
D13 | PD8 | I/O | FMC_NBL0
D14 | PD5 | I/O | USART2_TX
E1 | VDDA18PMU | Power
E2 | VSSAPMU | Power
E3 | PWR_ON | MonoIO
E4 | NRST | Reset
E5 | VDDA18AON | Power
E6 | PH2 | I/O
E7 | VSS | Power
E8 | VDDIO4 | Power
E9 | VDDIO4 | Power
E10 | PD2 | I/O | FMC_A0
E11 | PD12 | I/O | FMC_A5
E12 | PB3 | I/O | FMC_NBL1
E13 | PB2 | I/O | FMC_D2
E14 | PD13 | I/O | TIM4_CH2
F1 | VSSSMPS | Power
F2 | VSSSMPS | Power
F3 | VSSSMPS | Power
F4 | VSSSMPS | Power
F5 | VSSAON | Power
F10 | VSS | Power
F11 | PD11 | I/O | FMC_D8
F12 | PE0 | I/O | USART3_RX
F13 | PE1 | I/O | FMC_D10
F14 | PE2 | I/O | FMC_D11
G1 | VLXSMPS | Power
G2 | VLXSMPS | Power
G3 | VLXSMPS | Power
G4 | VLXSMPS | Power
G10 | VDD | Power
G11 | VDD | Power
G12 | VDD | Power
G13 | PE3 | I/O | FMC_D12
G14 | PB0 | I/O | FMC_D13
H1 | VDDSMPS | Power
H2 | VDDSMPS | Power
H3 | VDDSMPS | Power
H4 | VDDSMPS | Power
H10 | VSS | Power
H11 | VSS | Power
H12 | PD9 | I/O | FMC_SDCLK
H13 | PB7 | I/O | FMC_D15
H14 | PB6 | I/O | FMC_D14
J1 | PF4 | I/O | SPI1_NSS
J2 | PF6 | I/O | USART2_RX
J3 | PF10 | I/O
J4 | PF5 | I/O
J5 | PF3 | I/O
J10 | VDDIO3 | Power
J11 | VDDIO3 | Power
J12 | PN12 | I/O
J13 | PN4 | I/O | XSPIM_P2_IO2
J14 | PN8 | I/O | XSPIM_P2_IO4
K1 | PF2 | I/O
K2 | PF14 | I/O | TIM2_CH2
K3 | PF15 | I/O | SPI5_SCK
K4 | PF7 | I/O | TIM3_CH3
K5 | VSS | Power
K6 | VDDCORE | Power
K7 | VDDCORE | Power
K8 | VDDCORE | Power
K9 | VDDCORE | Power
K10 | VSS | Power
K11 | PA3 | I/O | SPI5_NSS
K12 | PN6 | I/O | XSPIM_P2_CLK
K13 | PN7 | I/O
K14 | PN5 | I/O | XSPIM_P2_IO3
L1 | PF8 | I/O
L2 | PF11 | I/O | SPI5_MOSI
L3 | PF12 | I/O | SPI5_MISO
L4 | VDDA18PLL | Power
L5 | PG14 | I/O
L6 | PA12 | I/O | FMC_D0
L7 | VDDCORE | Power
L8 | PA6 | I/O | BOOT1
L9 | PA1 | I/O | FMC_D6
L10 | PB11 | I/O | I2C2_SDA
L11 | PB4(NJTRST) | I/O | SPI1_MISO
L12 | PG8 | I/O | USART1_RX
L13 | PN2 | I/O | XSPIM_P2_IO0
L14 | PN9 | I/O | XSPIM_P2_IO5
M1 | VREF+ | MonoIO
M2 | PF13 | I/O | USART1_TX
M3 | VDDA18ADC | Power
M4 | VSSA | Power
M5 | PG15 | I/O | TIM1_CH4
M6 | PA11 | I/O | FMC_D1
M7 | PA9 | I/O | FMC_D3
M8 | PA5 | I/O | SPI1_SCK
M9 | PG1 | I/O
M10 | PB12 | I/O | FMC_D9
M11 | PB5(JTDO/TRACESWO) | I/O | SPI1_MOSI
M12 | PG0 | Output | GPIO_Output
M13 | PN0 | I/O | XSPIM_P2_DQS0
M14 | PN10 | I/O | XSPIM_P2_IO6
N1 | VREF- | Power
N2 | CSI_D1N | MonoIO
N3 | CSI_CKN | MonoIO
N4 | CSI_D0N | MonoIO
N5 | CSI_REXT | MonoIO
N6 | VDDCSI | Power
N7 | PA10 | I/O | TIM1_CH3
N8 | PA2 | I/O | FMC_D5
N9 | PG12 | Output | GPIO_Output
N10 | PG10 | Output | GPIO_Output
N11 | PG2 | Output | GPIO_Output
N12 | PA15(JTDI) | I/O | TIM2_CH1
N13 | PN3 | I/O | XSPIM_P2_IO1
N14 | PN11 | I/O | XSPIM_P2_IO7
P1 | VSS | Power
P2 | CSI_D1P | MonoIO
P3 | CSI_CKP | MonoIO
P4 | CSI_D0P | MonoIO
P5 | VDDA18CSI | Power
P6 | PA14(JTCK/SWCLK) | I/O | DEBUG_JTCK-SWCLK
P7 | PA13(JTMS/SWDIO) | I/O | DEBUG_JTMS-SWDIO
P8 | PA8 | I/O | FMC_D4
P9 | PG13 | I/O | TIM4_CH1
P10 | PA0 | I/O | FMC_D7
P11 | PB10 | I/O | I2C2_SCL
P12 | PA7 | I/O | HDP_HDP7
P13 | PN1 | I/O | XSPIM_P2_NCS1
P14 | VSS | Power

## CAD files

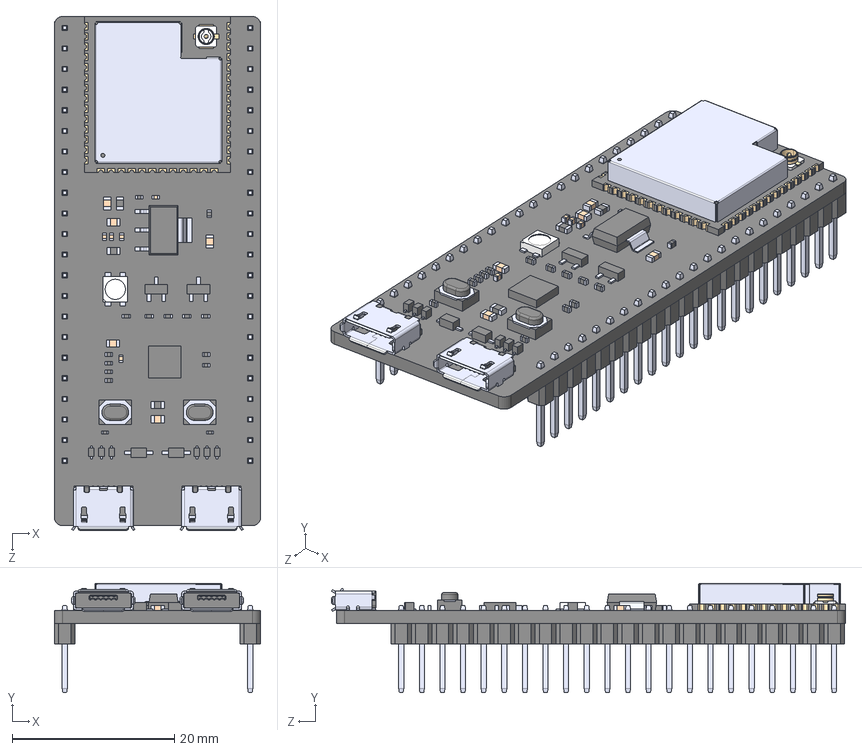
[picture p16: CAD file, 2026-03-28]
Hardware/Main_Board/3DModels/ESP32-S3-DEVKITC-1U-N8R2.step
25.4 x 13.5 x 63.3 mm

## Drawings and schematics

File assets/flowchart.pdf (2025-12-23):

# Flowchart for Project Completion

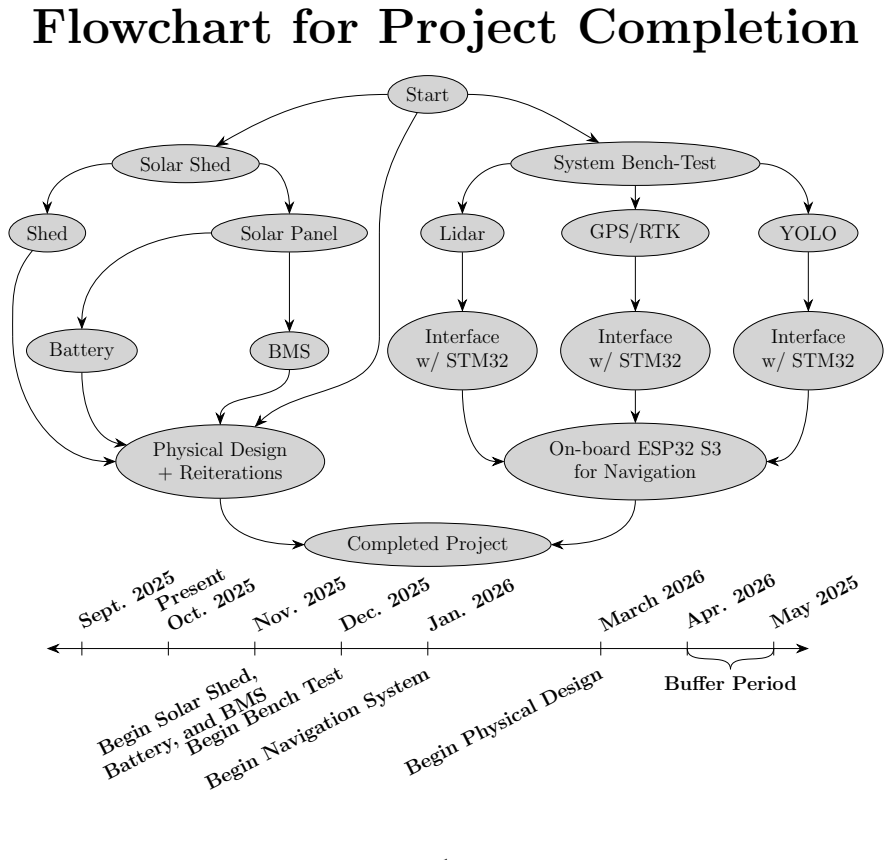
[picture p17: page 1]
Start; Solar Shed; Shed; Solar Panel; Battery; BMS; Lidar; GPS/RTK; YOLO; Interface w/ STM32; On-board ESP32 S3 for Navigation; Physical Design + Reiterations; Completed Project; Sept. 2025; May 2025; Present Oct. 2025; Nov. 2025 Dec. 2025 Jan. 2026; March 2026 Apr. 2026; Buffer Period

System Bench-Test

Begin Solar Shed,

Begin Bench Test

Begin Navigation System

Begin Physical Design

Battery, and BMS

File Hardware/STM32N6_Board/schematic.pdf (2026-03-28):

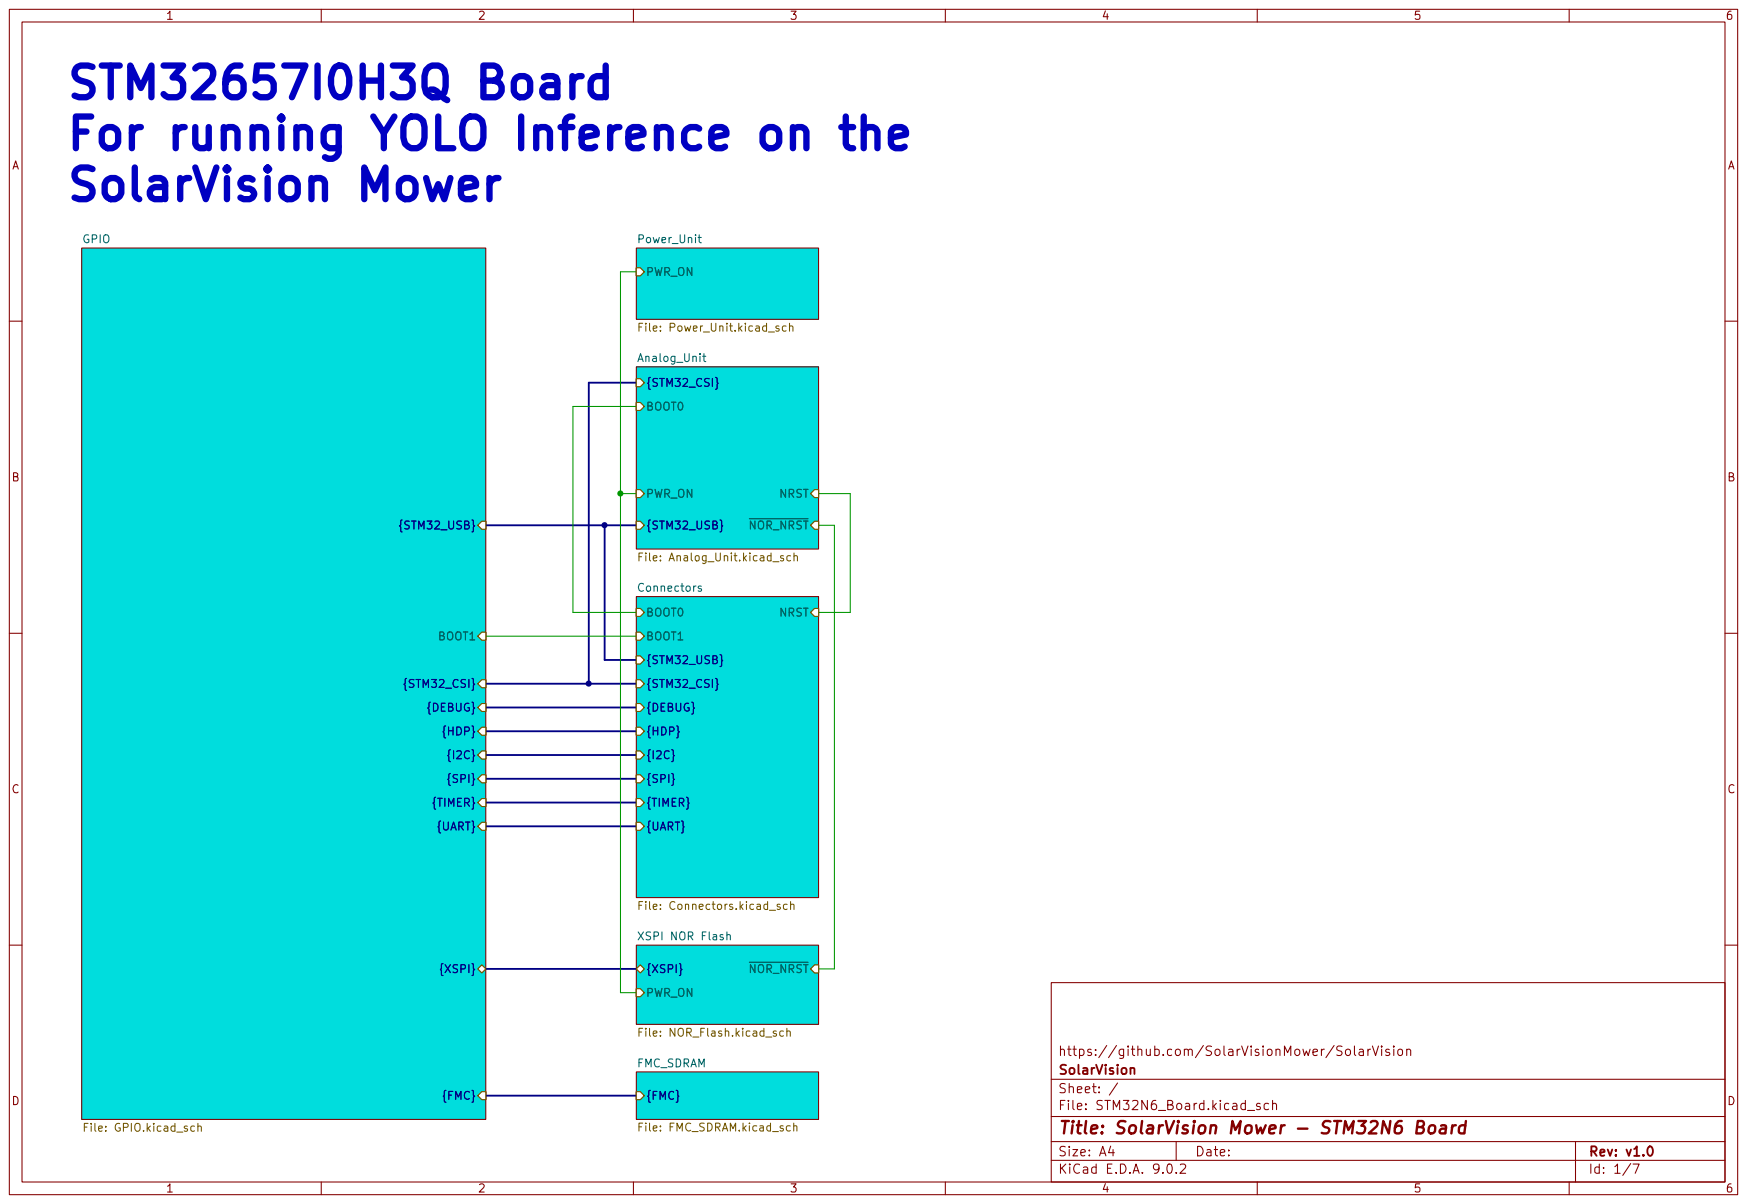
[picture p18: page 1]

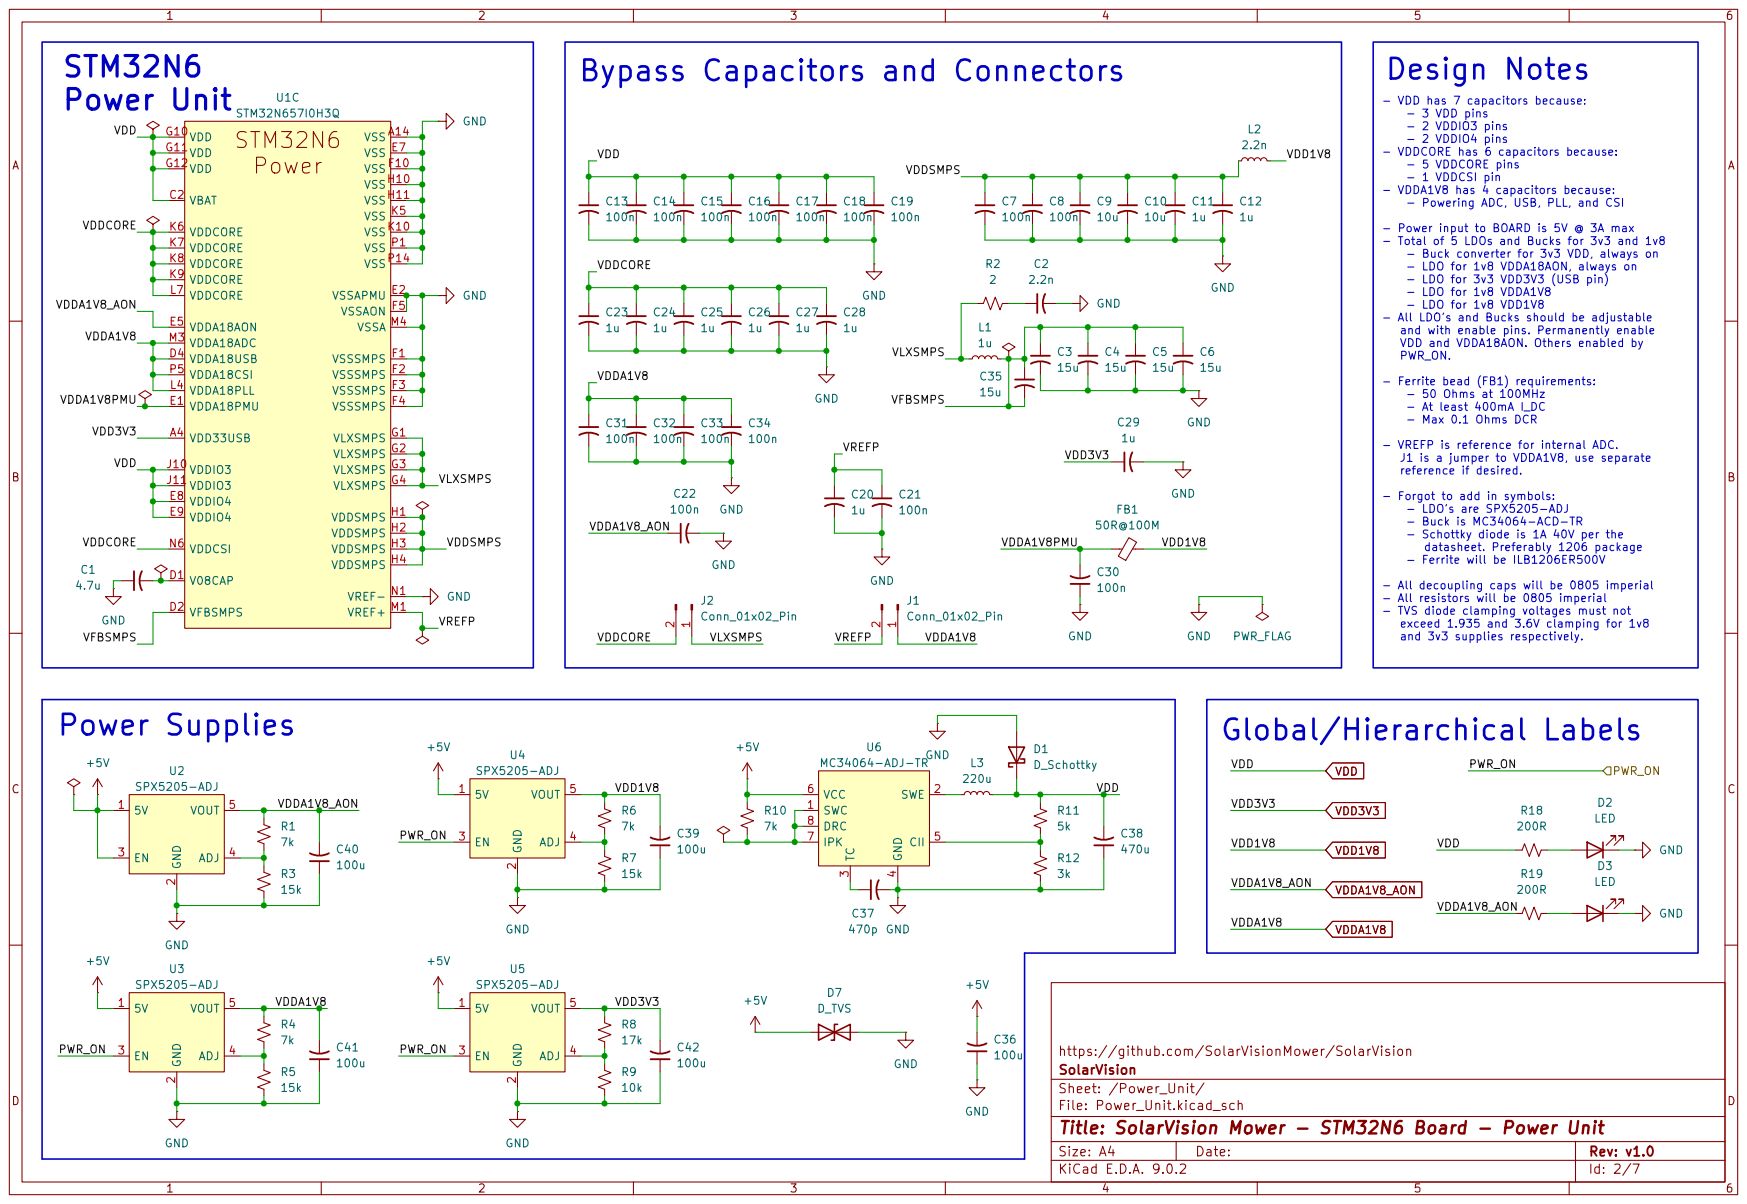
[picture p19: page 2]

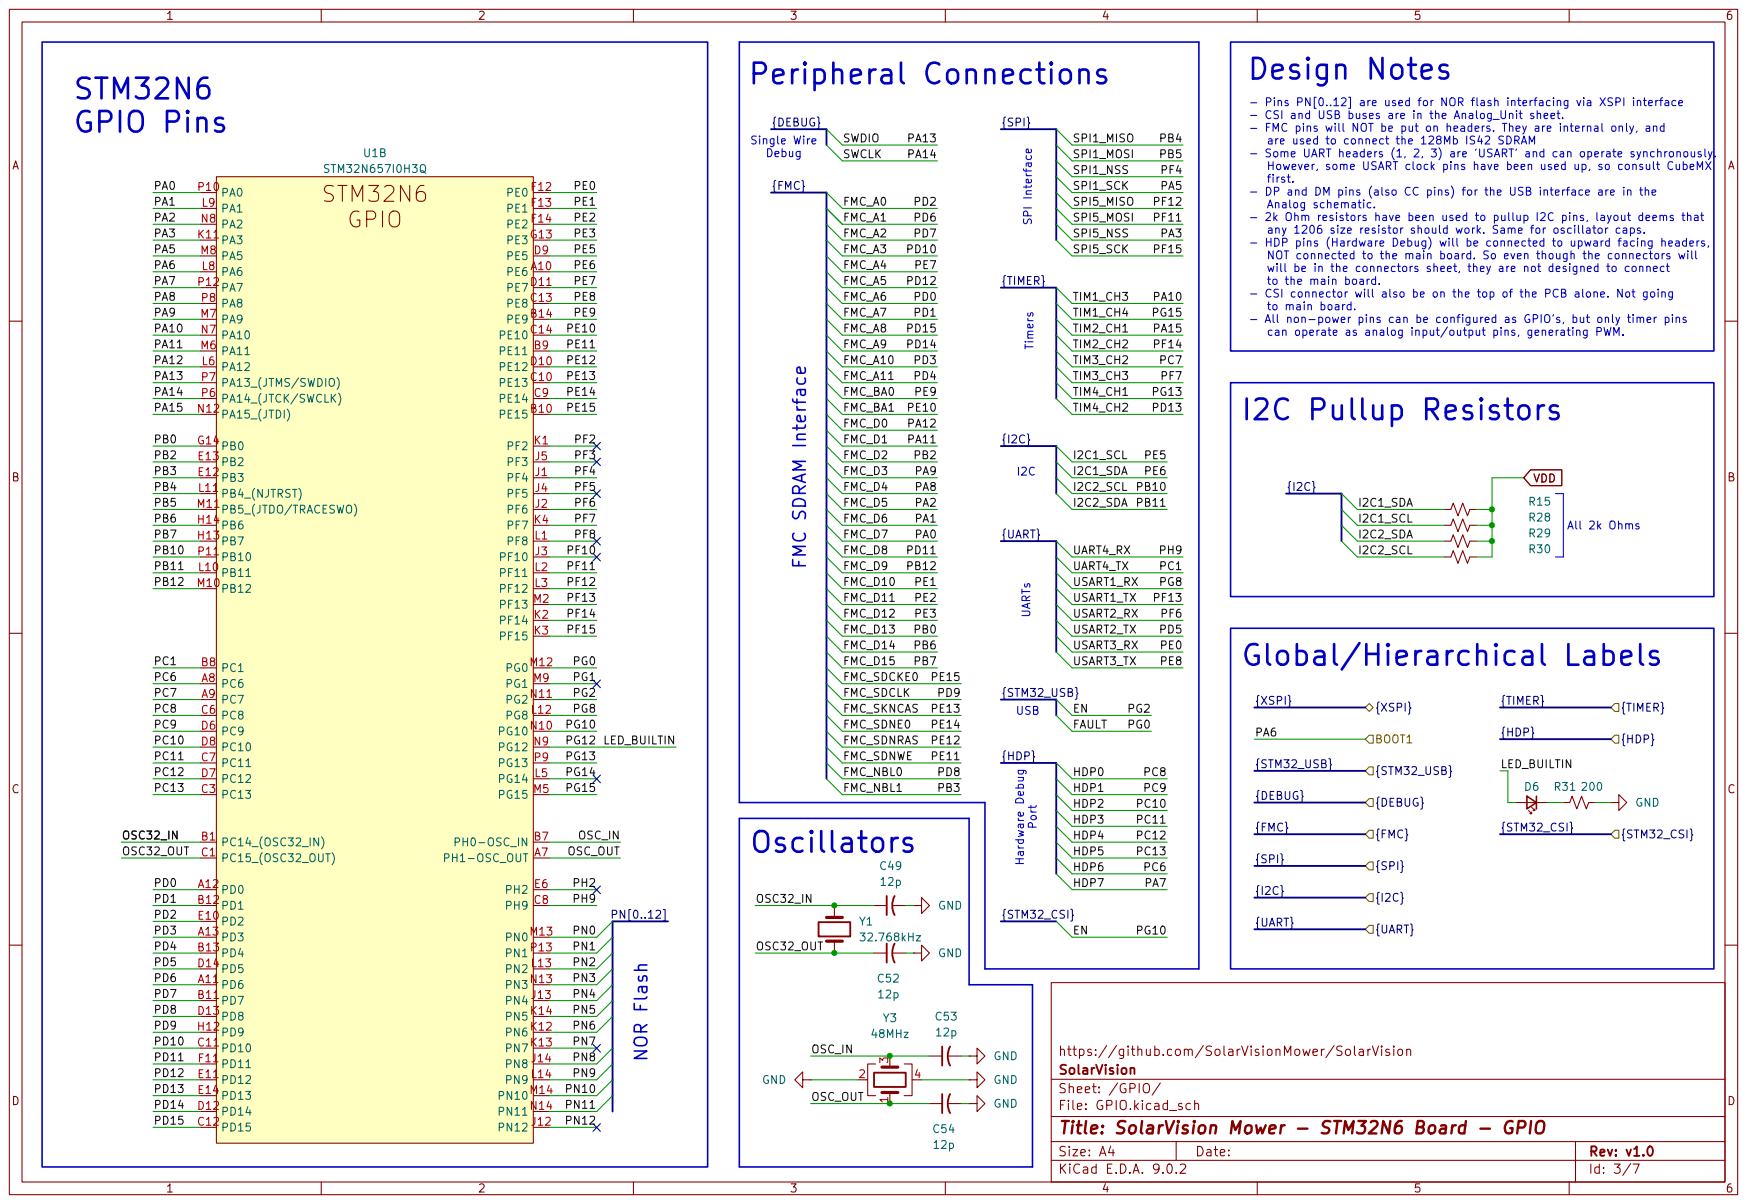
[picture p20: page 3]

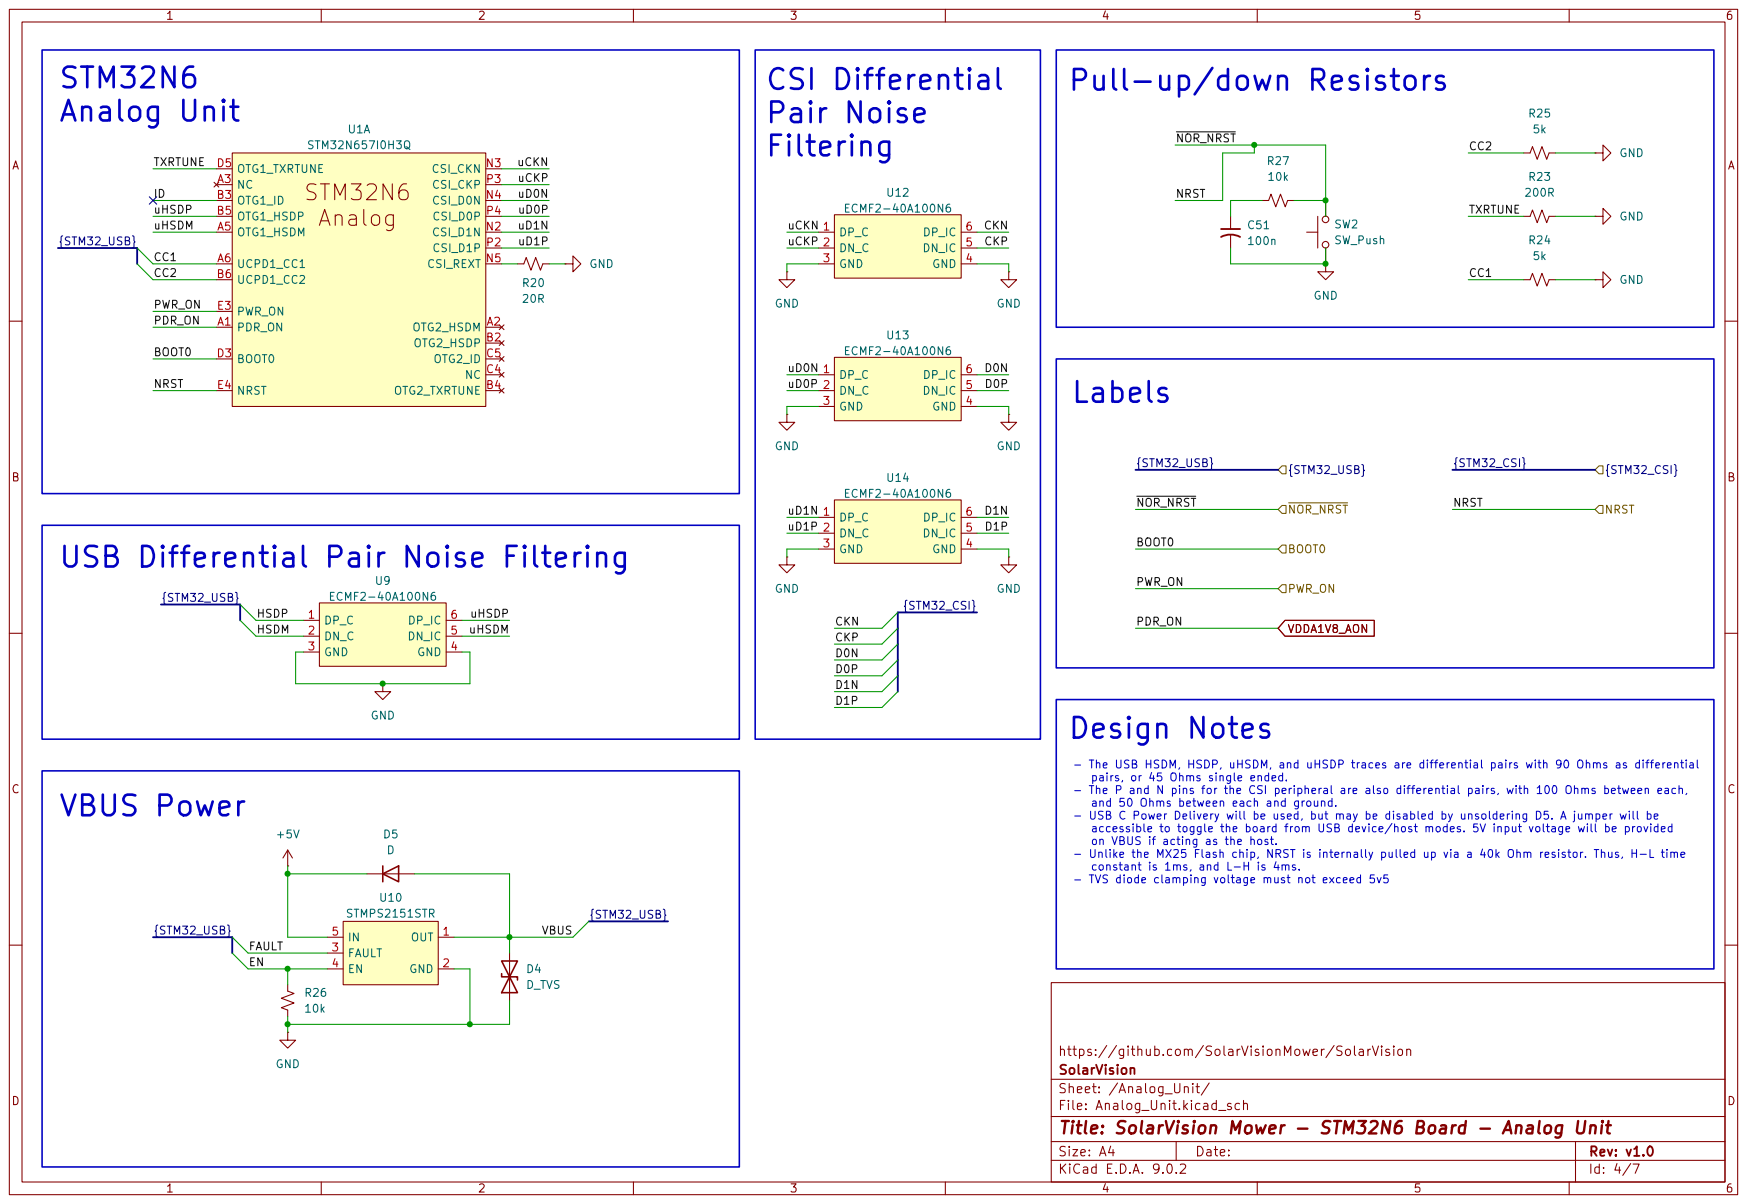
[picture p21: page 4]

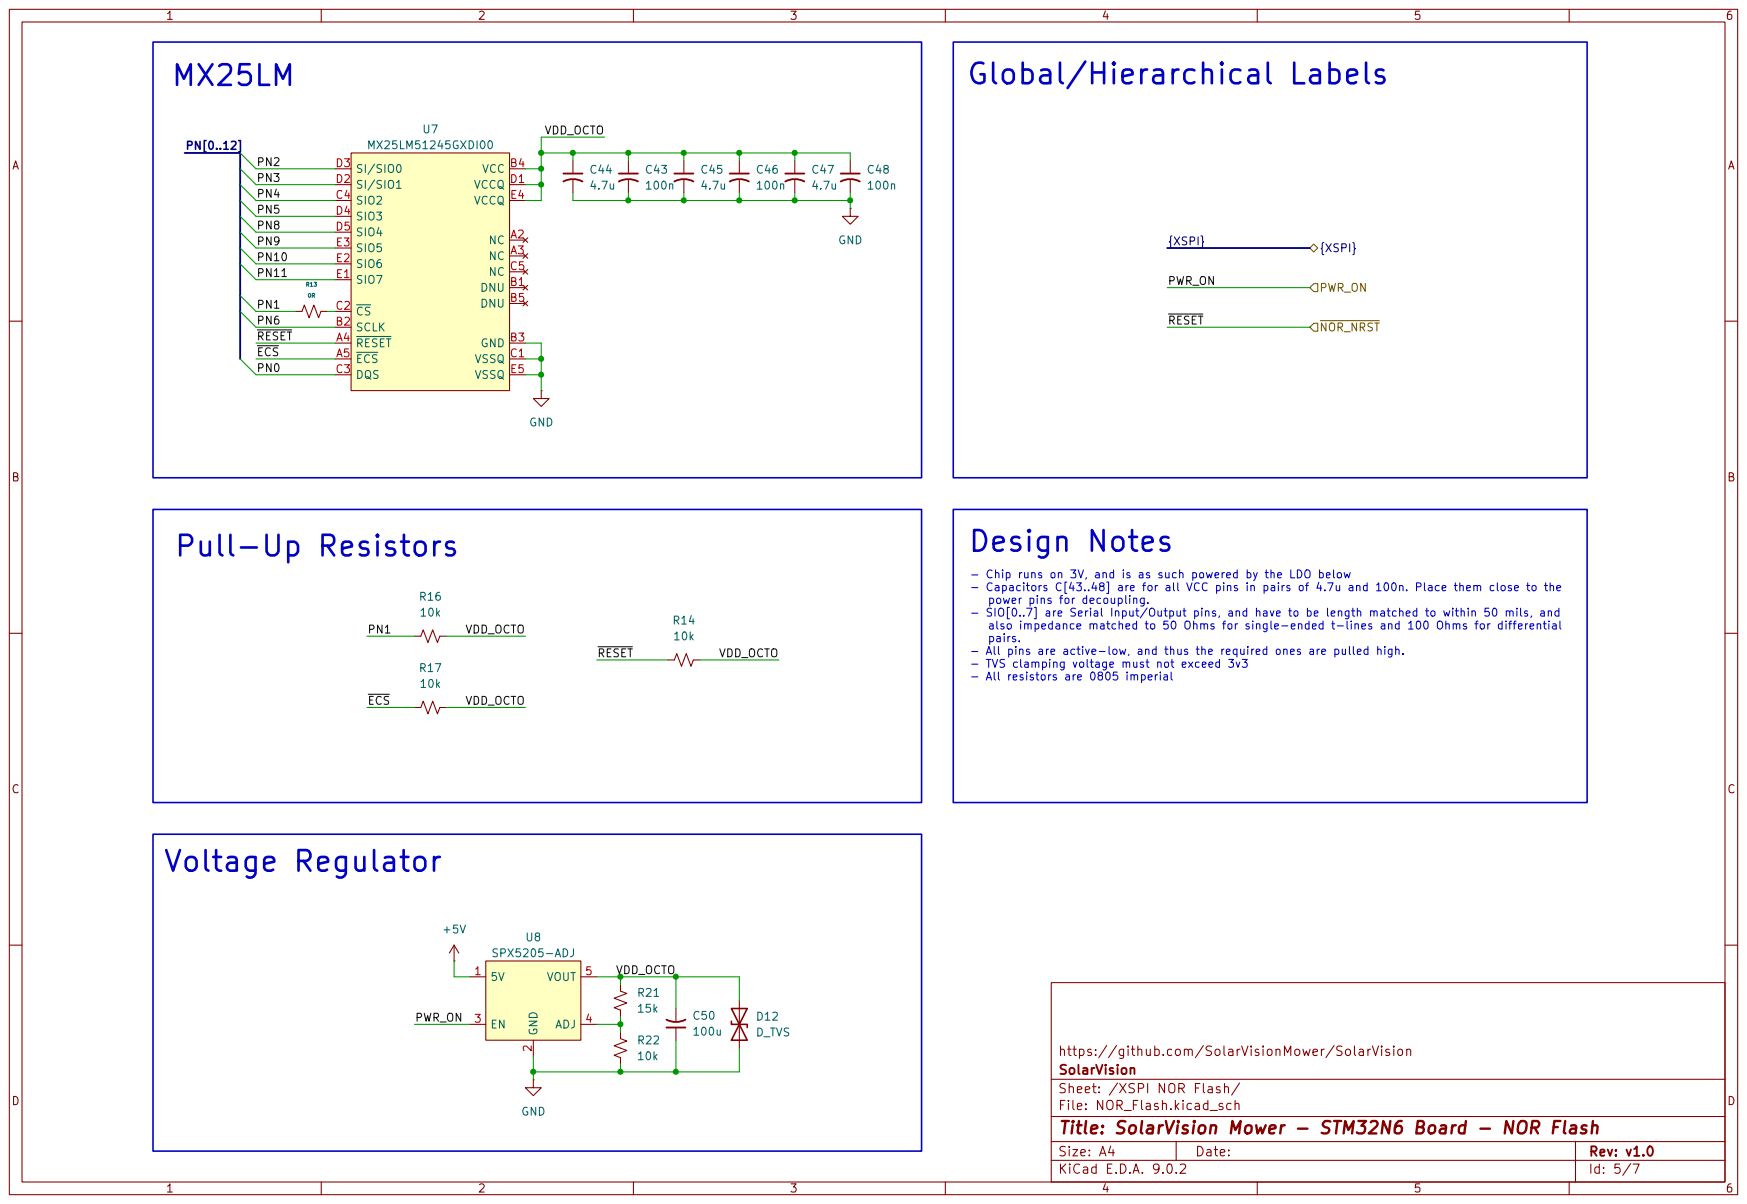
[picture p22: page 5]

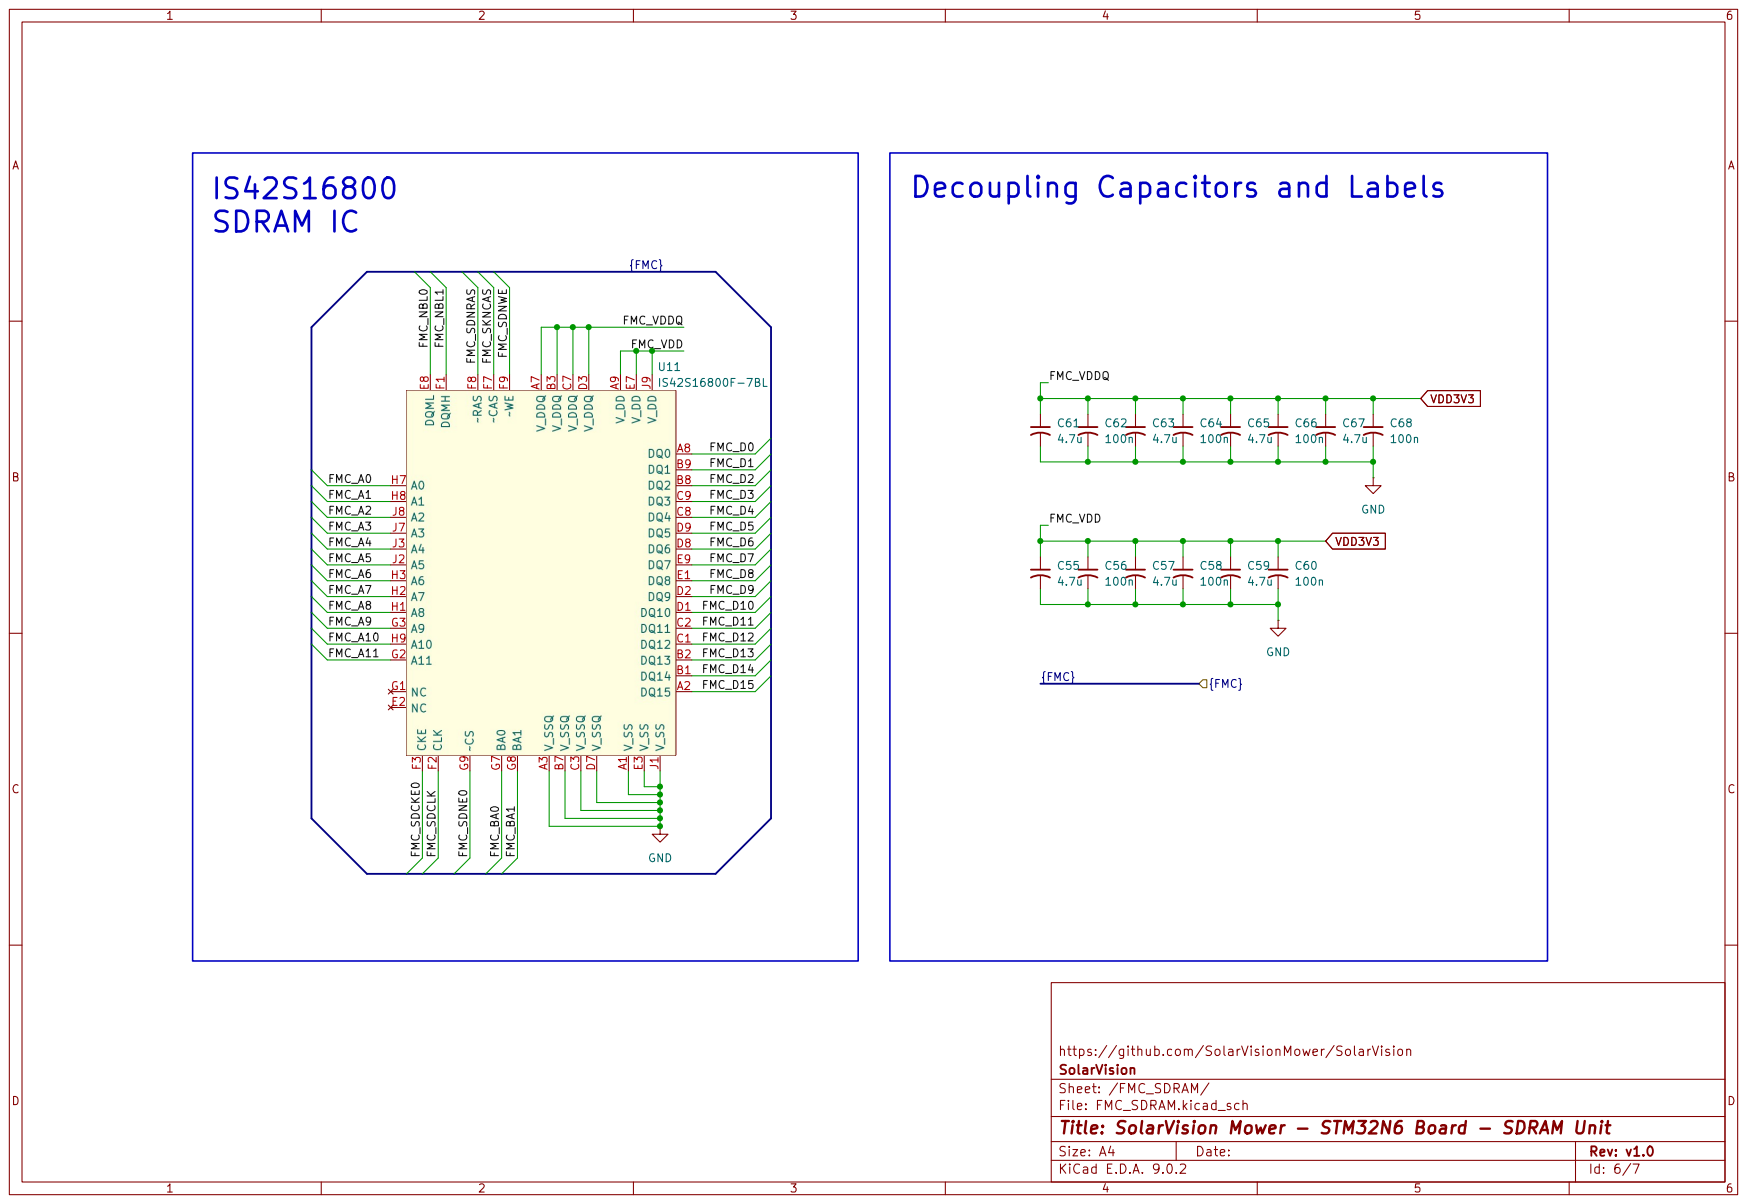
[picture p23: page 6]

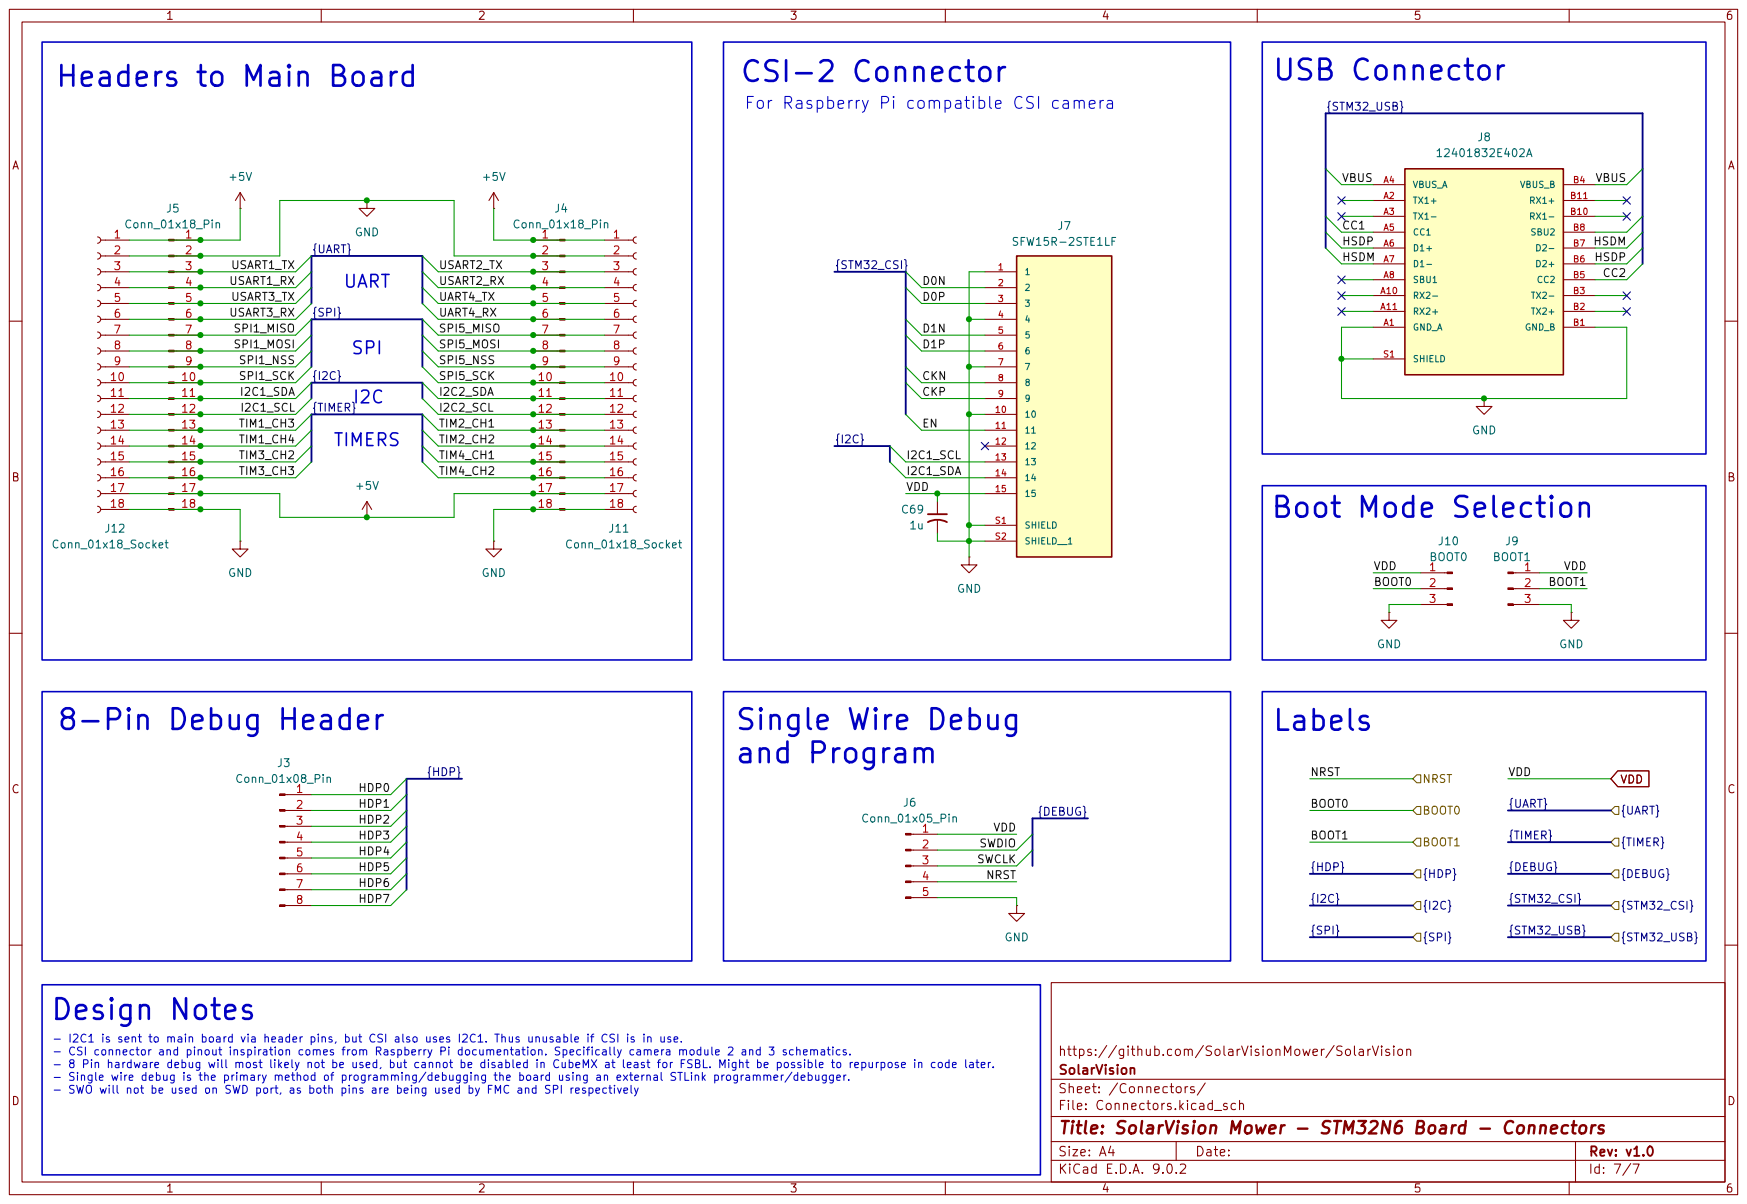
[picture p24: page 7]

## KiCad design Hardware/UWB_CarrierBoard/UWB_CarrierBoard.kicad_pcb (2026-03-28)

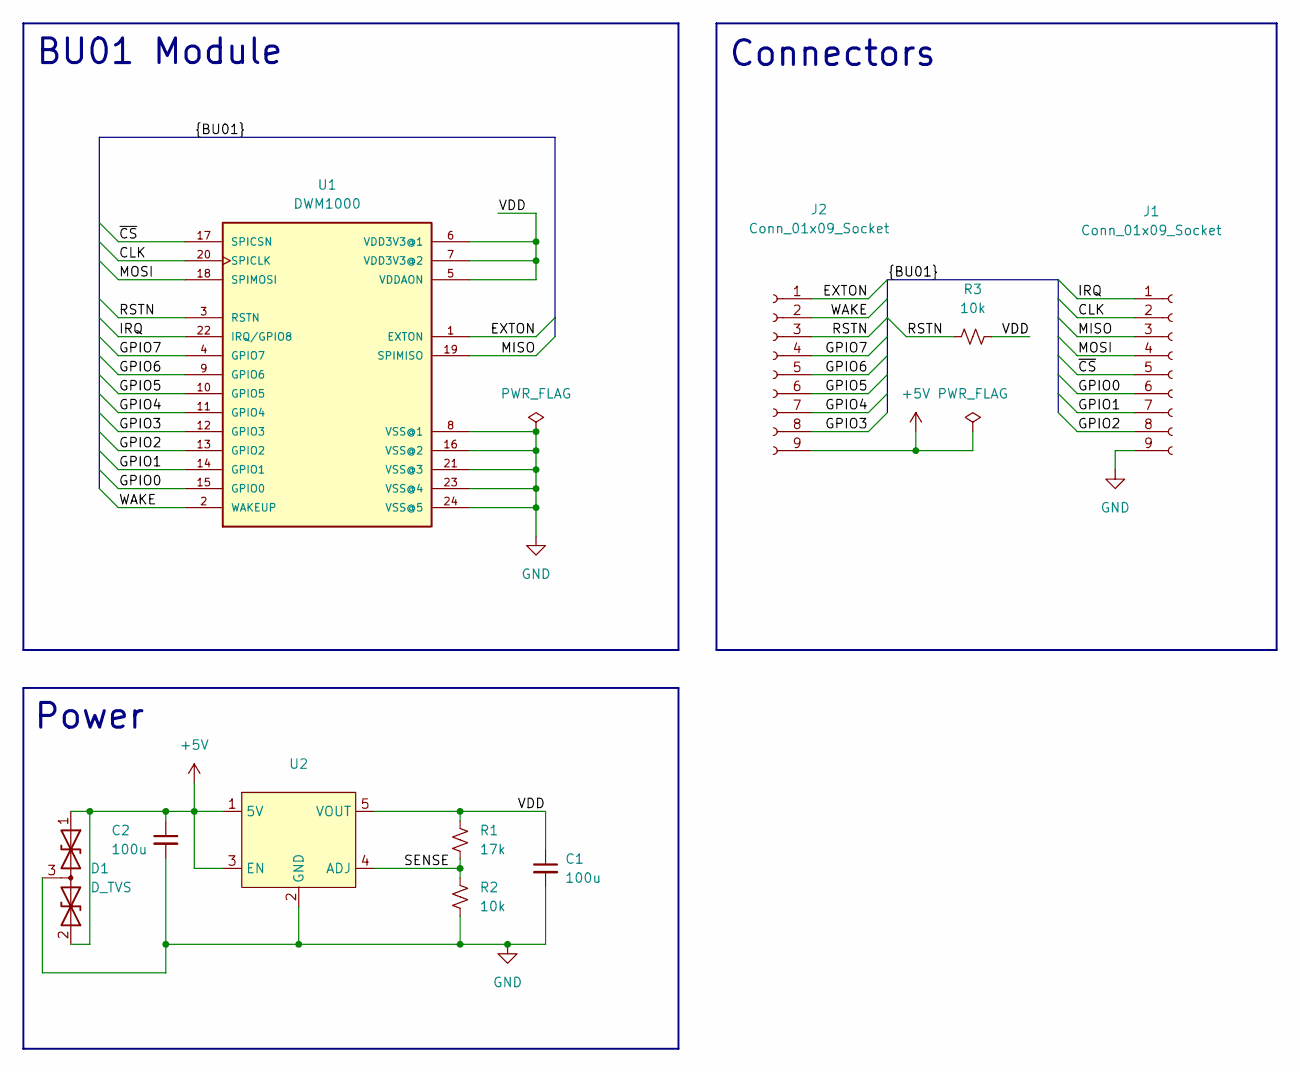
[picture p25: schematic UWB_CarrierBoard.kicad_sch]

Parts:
C1, C2: 100u; C_0402_1005Metric
D1: D_TVS; SOT-723
J1, J2: Conn_01x09_Socket; PinSocket_1x09_P2.54mm_Vertical
R1: 17k; R_0402_1005Metric
R2, R3: 10k; R_0402_1005Metric
U1: DWM1000; BU01
U2: SOT-23-5

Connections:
+5V: C2.1, D1.1 (A1), D1.2 (A2), J2.9, U2.1 (5V), U2.3 (EN)
/CLK: J1.2, U1.20 (SPICLK)
/EXTON: J2.1, U1.1 (EXTON)
/GPIO0: J1.6, U1.15 (GPIO0)
/GPIO1: J1.7, U1.14 (GPIO1)
/GPIO2: J1.8, U1.13 (GPIO2)
/GPIO3: J2.8, U1.12 (GPIO3)
/GPIO4: J2.7, U1.11 (GPIO4)
/GPIO5: J2.6, U1.10 (GPIO5)
/GPIO6: J2.5, U1.9 (GPIO6)
/GPIO7: J2.4, U1.4 (GPIO7)
/IRQ: J1.1, U1.22 (IRQ/GPIO8)
/MISO: J1.3, U1.19 (SPIMISO)
/MOSI: J1.4, U1.18 (SPIMOSI)
/RSTN: J2.3, R3.1, U1.3 (RSTN)
/SENSE: R1.2, R2.1, U2.4 (ADJ)
/VDD: C1.1, R1.1, R3.2, U1.5 (VDDAON), U1.6 (VDD3V3@1), U1.7 (VDD3V3@2), U2.5 (VOUT)
/WAKE: J2.2, U1.2 (WAKEUP)
/~CS: J1.5, U1.17 (SPICSN)
GND: C1.2, C2.2, D1.3 (common), J1.9, R2.2, U1.8 (VSS@1), U1.16 (VSS@2), U1.21 (VSS@3), U1.23 (VSS@4), U1.24 (VSS@5), U2.2 (GND)

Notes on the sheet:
Connectors
BU01 Module
Power

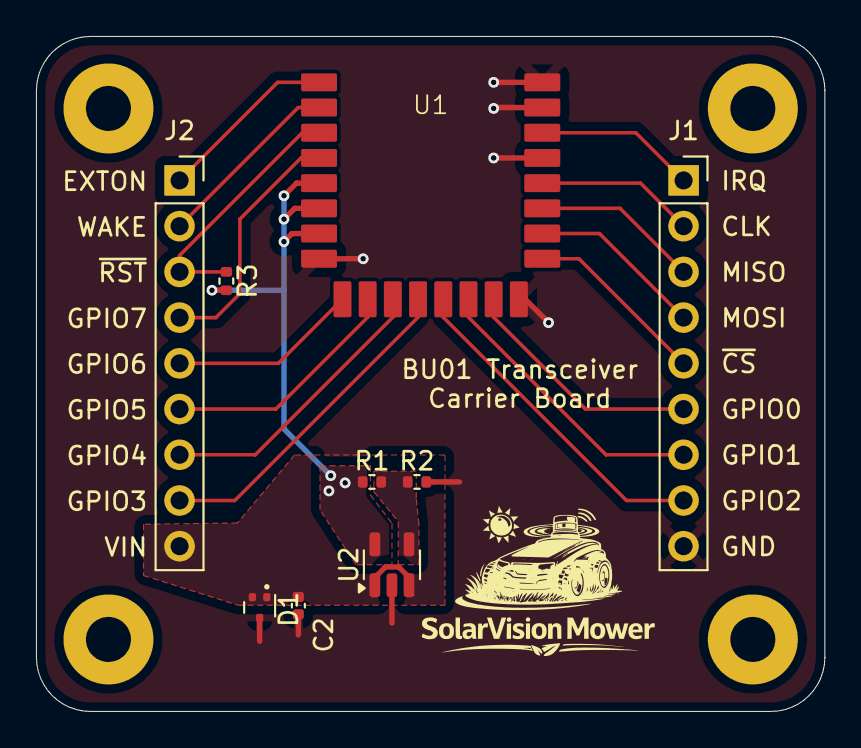
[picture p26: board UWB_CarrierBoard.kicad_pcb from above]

Board: 2 copper layers, 43.8 x 37.5 mm, 10 parts (1 on the bottom side), 20 nets.

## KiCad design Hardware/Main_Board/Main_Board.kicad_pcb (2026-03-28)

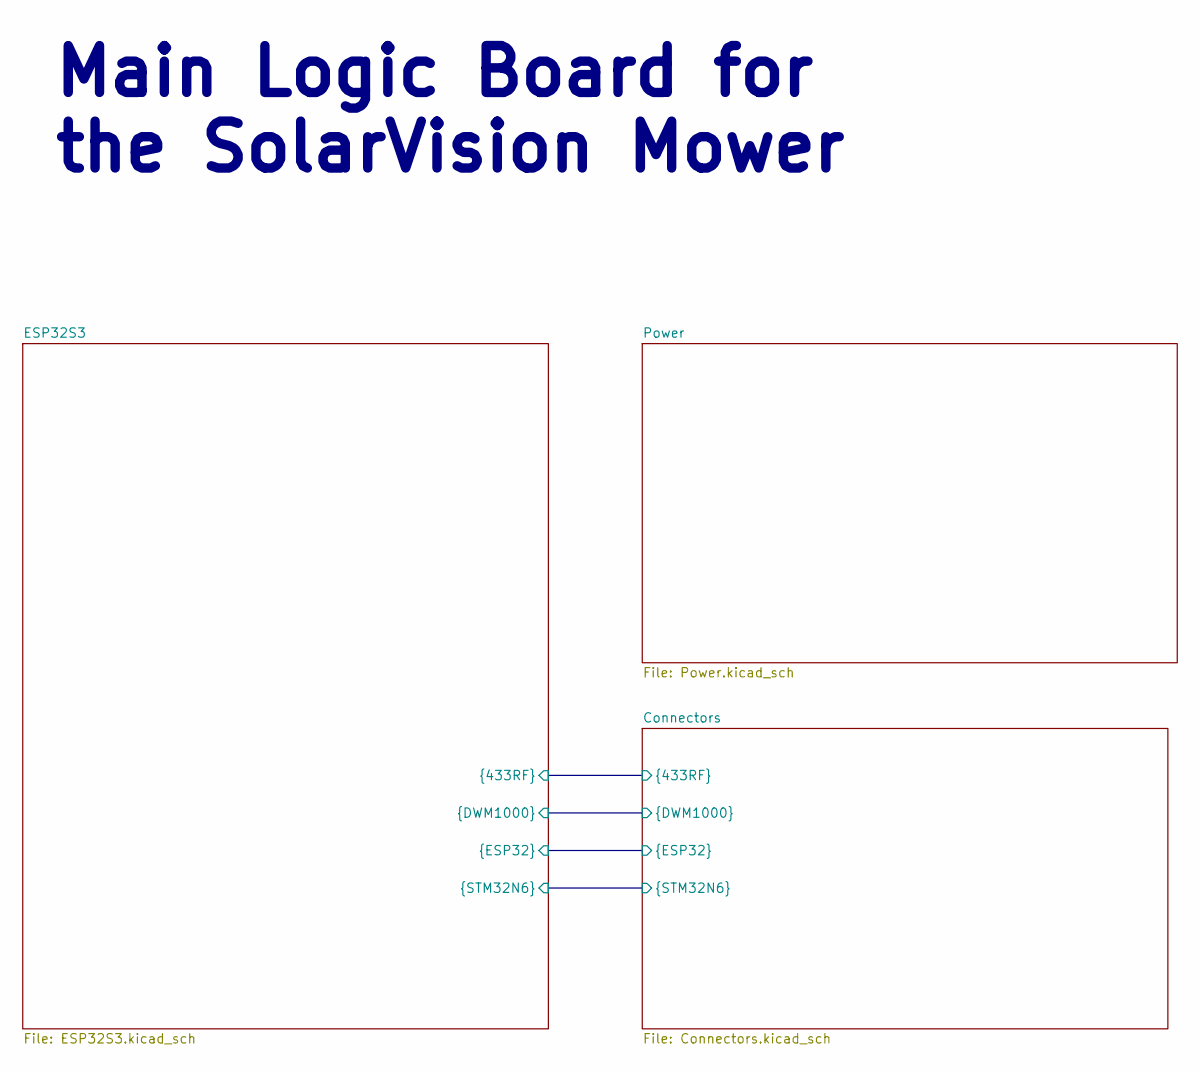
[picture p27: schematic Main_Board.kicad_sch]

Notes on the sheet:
Main Logic Board for the SolarVision Mower

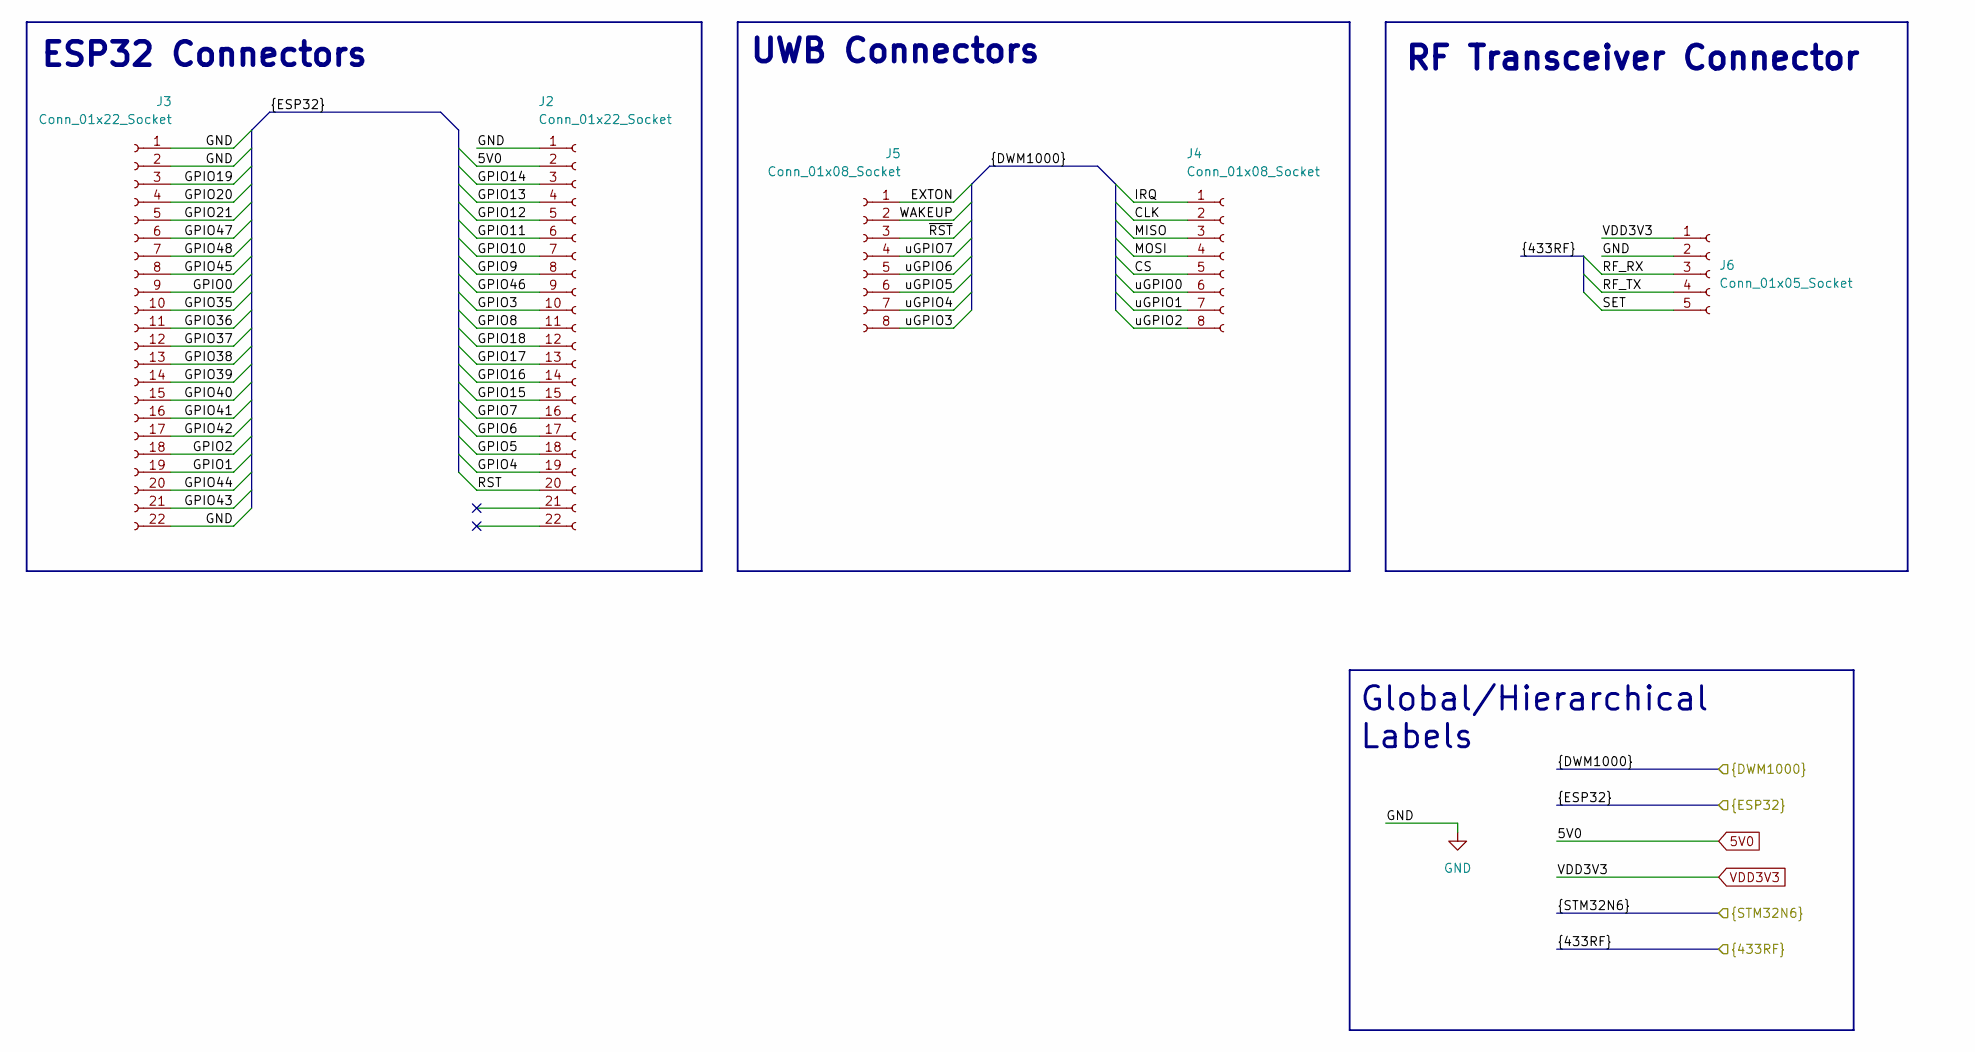
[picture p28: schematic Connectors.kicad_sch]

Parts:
J2, J3: Conn_01x22_Socket; PinSocket_1x22_P2.54mm_Vertical
J4, J5: Conn_01x08_Socket; PinSocket_1x08_P2.54mm_Vertical
J6: Conn_01x05_Socket; PinSocket_1x05_P2.54mm_Vertical

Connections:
5V0: J2.2; also elsewhere on the board
/Connectors/EXTON: J5.1; also elsewhere on the board
/Connectors/GPIO0: J3.9; also elsewhere on the board
/Connectors/GPIO1: J3.19; also elsewhere on the board
/Connectors/GPIO2: J3.18; also elsewhere on the board
/Connectors/GPIO3: J2.10; also elsewhere on the board
/Connectors/GPIO4: J2.19; also elsewhere on the board
/Connectors/GPIO5: J2.18, J6.5; also elsewhere on the board
/Connectors/GPIO6: J2.17, J6.4; also elsewhere on the board
/Connectors/GPIO7: J2.16, J6.3; also elsewhere on the board
/Connectors/GPIO8: J2.11; also elsewhere on the board
/Connectors/GPIO9: J2.8; also elsewhere on the board
/Connectors/GPIO10: J2.7, J4.5; also elsewhere on the board
/Connectors/GPIO11: J2.6, J4.4; also elsewhere on the board
/Connectors/GPIO12: J2.5, J4.2; also elsewhere on the board
/Connectors/GPIO13: J2.4, J4.3; also elsewhere on the board
/Connectors/GPIO14: J2.3; also elsewhere on the board
/Connectors/GPIO15: J2.15; also elsewhere on the board
/Connectors/GPIO16: J2.14; also elsewhere on the board
/Connectors/GPIO17: J2.13; also elsewhere on the board
/Connectors/GPIO18: J2.12; also elsewhere on the board
/Connectors/GPIO19: J3.3; also elsewhere on the board
/Connectors/GPIO20: J3.4; also elsewhere on the board
/Connectors/GPIO21: J3.5; also elsewhere on the board
/Connectors/GPIO35: J3.10; also elsewhere on the board
/Connectors/GPIO36: J3.11; also elsewhere on the board
/Connectors/GPIO37: J3.12; also elsewhere on the board
/Connectors/GPIO38: J3.13; also elsewhere on the board
/Connectors/GPIO39: J3.14; also elsewhere on the board
/Connectors/GPIO40: J3.15; also elsewhere on the board
/Connectors/GPIO41: J3.16; also elsewhere on the board
/Connectors/GPIO42: J3.17; also elsewhere on the board
/Connectors/GPIO43: J3.21; also elsewhere on the board
/Connectors/GPIO44: J3.20; also elsewhere on the board
/Connectors/GPIO45: J3.8; also elsewhere on the board
/Connectors/GPIO46: J2.9; also elsewhere on the board
/Connectors/IRQ: J4.1; also elsewhere on the board
/Connectors/RST: J2.20; also elsewhere on the board
/Connectors/RX1: J3.6; also elsewhere on the board
/Connectors/TX1: J3.7; also elsewhere on the board
/Connectors/WAKEUP: J5.2; also elsewhere on the board
/Connectors/uGPIO0: J4.6; also elsewhere on the board
/Connectors/uGPIO1: J4.7; also elsewhere on the board
/Connectors/uGPIO2: J4.8; also elsewhere on the board
/Connectors/uGPIO3: J5.8; also elsewhere on the board
/Connectors/uGPIO4: J5.7; also elsewhere on the board
/Connectors/uGPIO5: J5.6; also elsewhere on the board
/Connectors/uGPIO6: J5.5; also elsewhere on the board
/Connectors/uGPIO7: J5.4; also elsewhere on the board
/Connectors/~RST: J5.3; also elsewhere on the board
GND: J2.1, J3.1, J3.2, J3.22, J6.2; also elsewhere on the board

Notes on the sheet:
ESP32 Connectors
RF Transceiver Connector
UWB Connectors
Global/Hierarchical Labels

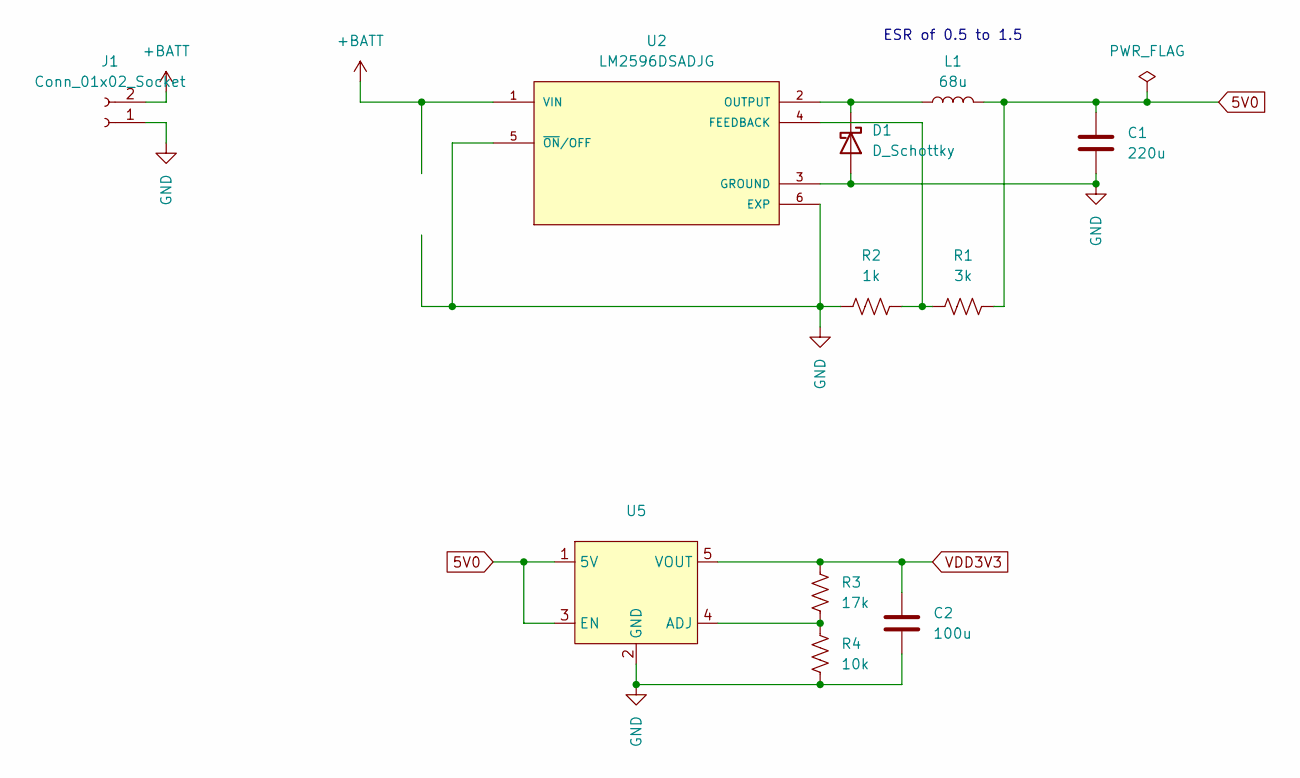
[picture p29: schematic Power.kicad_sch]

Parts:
C1: 220u; CP_Radial_D4.0mm_P1.50mm
C2: 100u; C_0805_2012Metric
D1: D_Schottky; C_0805_2012Metric
J1: Conn_01x02_Socket; TerminalBlock_bornier-2_P5.08mm
L1: 68u; L_0805_2012Metric
R1: 3k; R_0603_1608Metric
R2: 1k; R_0603_1608Metric
R3: 17k; R_0603_1608Metric
R4: 10k; R_0603_1608Metric
U2: LM2596DSADJG; CONV_LM2596DSADJG; PARTREV 0
U5: SOT-23-5

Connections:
5V0: C1.1, L1.2, R1.2, U5.1 (5V), U5.3 (EN); also elsewhere on the board
+BATT: J1.2, U2.1 (VIN)
GND: C1.2, C2.2, D1.2 (A), J1.1, R2.1, R4.1, U2.3 (GROUND), U2.5 (~ON/OFF), U2.6 (EXP), U5.2 (GND); also elsewhere on the board
unnamed: D1.1 (K), L1.1, U2.2 (OUTPUT)
unnamed: R1.1, R2.2, U2.4 (FEEDBACK)
unnamed: R3.1, R4.2, U5.4 (ADJ)

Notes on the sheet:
ESR of 0.5 to 1.5

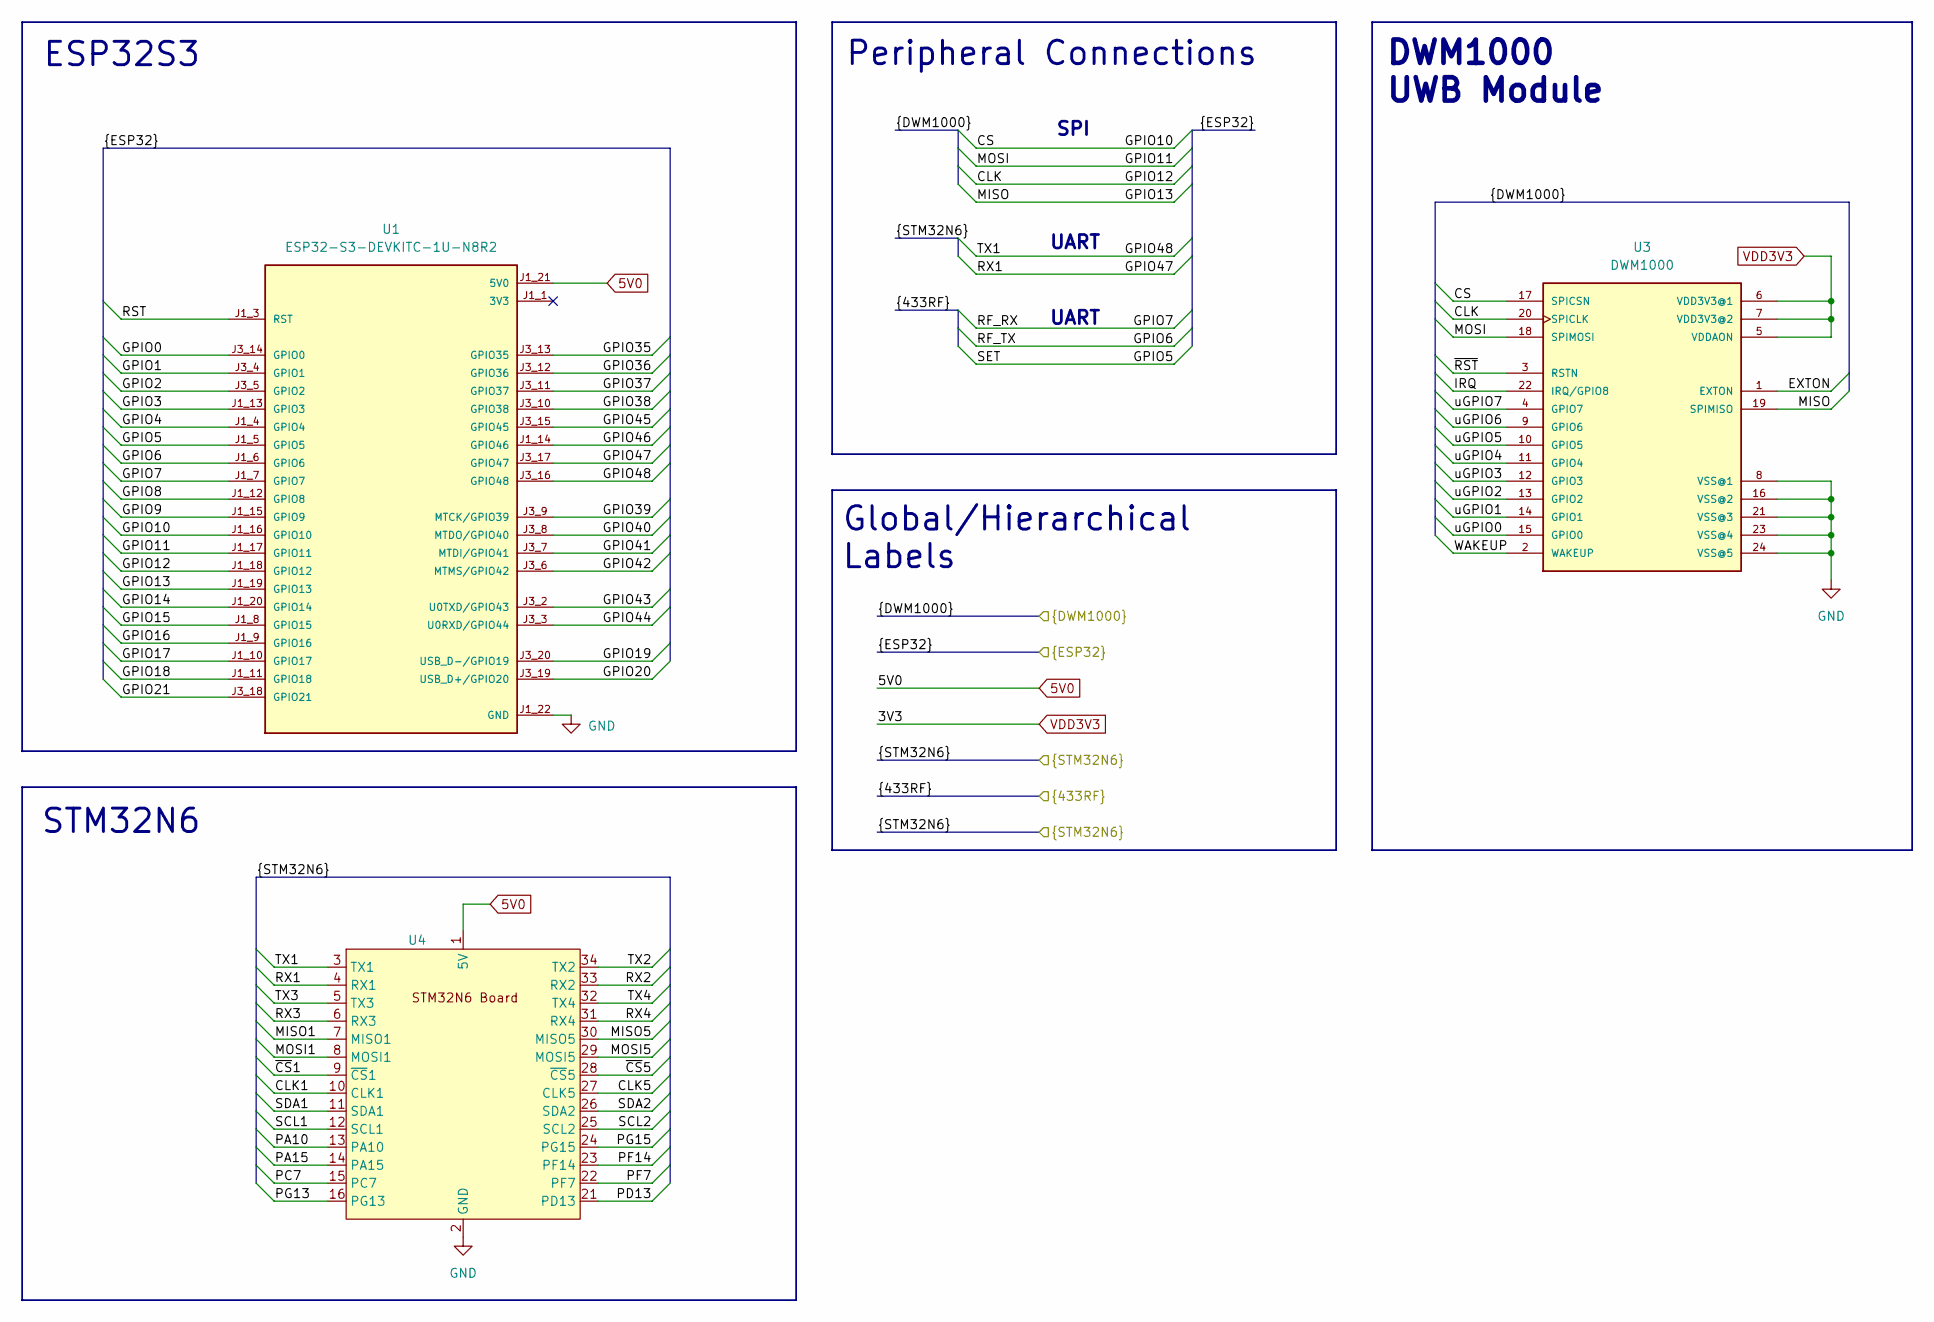
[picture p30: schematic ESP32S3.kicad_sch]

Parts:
U1: ESP32-S3-DEVKITC-1U-N8R2; XCVR_ESP32-S3-DEVKITC-1U-N8R2; PARTREV 5.3
U3: DWM1000; BU01
U4: STM32N6_Board

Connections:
5V0: U1.J1_21 (5V0), U4.1 (5V), U4.17 (5V), U4.20 (5V), U4.36 (5V); also elsewhere on the board
/Connectors/CLK1: U4.10 (CLK1)
/Connectors/CLK5: U4.27 (CLK5)
/Connectors/EXTON: U3.1 (EXTON); also elsewhere on the board
/Connectors/GPIO0: U1.J3_14 (GPIO0); also elsewhere on the board
/Connectors/GPIO1: U1.J3_4 (GPIO1); also elsewhere on the board
/Connectors/GPIO2: U1.J3_5 (GPIO2); also elsewhere on the board
/Connectors/GPIO3: U1.J1_13 (GPIO3); also elsewhere on the board
/Connectors/GPIO4: U1.J1_4 (GPIO4); also elsewhere on the board
/Connectors/GPIO5: U1.J1_5 (GPIO5); also elsewhere on the board
/Connectors/GPIO6: U1.J1_6 (GPIO6); also elsewhere on the board
/Connectors/GPIO7: U1.J1_7 (GPIO7); also elsewhere on the board
/Connectors/GPIO8: U1.J1_12 (GPIO8); also elsewhere on the board
/Connectors/GPIO9: U1.J1_15 (GPIO9); also elsewhere on the board
/Connectors/GPIO10: U1.J1_16 (GPIO10), U3.17 (SPICSN); also elsewhere on the board
/Connectors/GPIO11: U1.J1_17 (GPIO11), U3.18 (SPIMOSI); also elsewhere on the board
/Connectors/GPIO12: U1.J1_18 (GPIO12), U3.20 (SPICLK); also elsewhere on the board
/Connectors/GPIO13: U1.J1_19 (GPIO13), U3.19 (SPIMISO); also elsewhere on the board
/Connectors/GPIO14: U1.J1_20 (GPIO14); also elsewhere on the board
/Connectors/GPIO15: U1.J1_8 (GPIO15); also elsewhere on the board
/Connectors/GPIO16: U1.J1_9 (GPIO16); also elsewhere on the board
/Connectors/GPIO17: U1.J1_10 (GPIO17); also elsewhere on the board
/Connectors/GPIO18: U1.J1_11 (GPIO18); also elsewhere on the board
/Connectors/GPIO19: U1.J3_20 (USB_D-/GPIO19); also elsewhere on the board
/Connectors/GPIO20: U1.J3_19 (USB_D+/GPIO20); also elsewhere on the board
/Connectors/GPIO21: U1.J3_18 (GPIO21); also elsewhere on the board
/Connectors/GPIO35: U1.J3_13 (GPIO35); also elsewhere on the board
/Connectors/GPIO36: U1.J3_12 (GPIO36); also elsewhere on the board
/Connectors/GPIO37: U1.J3_11 (GPIO37); also elsewhere on the board
/Connectors/GPIO38: U1.J3_10 (GPIO38); also elsewhere on the board
/Connectors/GPIO39: U1.J3_9 (MTCK/GPIO39); also elsewhere on the board
/Connectors/GPIO40: U1.J3_8 (MTDO/GPIO40); also elsewhere on the board
/Connectors/GPIO41: U1.J3_7 (MTDI/GPIO41); also elsewhere on the board
/Connectors/GPIO42: U1.J3_6 (MTMS/GPIO42); also elsewhere on the board
/Connectors/GPIO43: U1.J3_2 (U0TXD/GPIO43); also elsewhere on the board
/Connectors/GPIO44: U1.J3_3 (U0RXD/GPIO44); also elsewhere on the board
/Connectors/GPIO45: U1.J3_15 (GPIO45); also elsewhere on the board
/Connectors/GPIO46: U1.J1_14 (GPIO46); also elsewhere on the board
/Connectors/IRQ: U3.22 (IRQ/GPIO8); also elsewhere on the board
/Connectors/MISO1: U4.7 (MISO1)
/Connectors/MISO5: U4.30 (MISO5)
/Connectors/MOSI1: U4.8 (MOSI1)
/Connectors/MOSI5: U4.29 (MOSI5)
/Connectors/PA10: U4.13 (PA10)
/Connectors/PA15: U4.14 (PA15)
/Connectors/PC7: U4.15 (PC7)
/Connectors/PD13: U4.21 (PD13)
/Connectors/PF7: U4.22 (PF7)
/Connectors/PF14: U4.23 (PF14)
/Connectors/PG13: U4.16 (PG13)
/Connectors/PG15: U4.24 (PG15)
/Connectors/RST: U1.J1_3 (RST); also elsewhere on the board
/Connectors/RX1: U1.J3_17 (GPIO47), U4.4 (RX1); also elsewhere on the board
/Connectors/RX2: U4.33 (RX2)
/Connectors/RX3: U4.6 (RX3)
/Connectors/RX4: U4.31 (RX4)
/Connectors/SCL1: U4.12 (SCL1)
/Connectors/SCL2: U4.25 (SCL2)
/Connectors/SDA1: U4.11 (SDA1)
/Connectors/SDA2: U4.26 (SDA2)
/Connectors/TX1: U1.J3_16 (GPIO48), U4.3 (TX1); also elsewhere on the board
/Connectors/TX2: U4.34 (TX2)
/Connectors/TX3: U4.5 (TX3)
/Connectors/TX4: U4.32 (TX4)
/Connectors/WAKEUP: U3.2 (WAKEUP); also elsewhere on the board
/Connectors/uGPIO0: U3.15 (GPIO0); also elsewhere on the board
/Connectors/uGPIO1: U3.14 (GPIO1); also elsewhere on the board
/Connectors/uGPIO2: U3.13 (GPIO2); also elsewhere on the board
/Connectors/uGPIO3: U3.12 (GPIO3); also elsewhere on the board
/Connectors/uGPIO4: U3.11 (GPIO4); also elsewhere on the board
/Connectors/uGPIO5: U3.10 (GPIO5); also elsewhere on the board
/Connectors/uGPIO6: U3.9 (GPIO6); also elsewhere on the board
/Connectors/uGPIO7: U3.4 (GPIO7); also elsewhere on the board
/Connectors/~CS1: U4.9 (~CS1)
/Connectors/~CS5: U4.28 (~CS5)
/Connectors/~RST: U3.3 (RSTN); also elsewhere on the board
GND: U1.J1_22 (GND), U1.J3_1 (GND), U1.J3_21 (GND), U1.J3_22 (GND), U3.8 (VSS@1), U3.16 (VSS@2), U3.21 (VSS@3), U3.23 (VSS@4), U3.24 (VSS@5), U4.2 (GND), U4.18 (GND), U4.19 (GND), U4.35 (GND), U4.GND1 (GND), U4.GND2 (GND), U4.GND3 (GND), U4.GND4 (GND); also elsewhere on the board

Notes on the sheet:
DWM1000 UWB Module
STM32N6
UART
SPI
ESP32S3
Peripheral Connections
Global/Hierarchical Labels

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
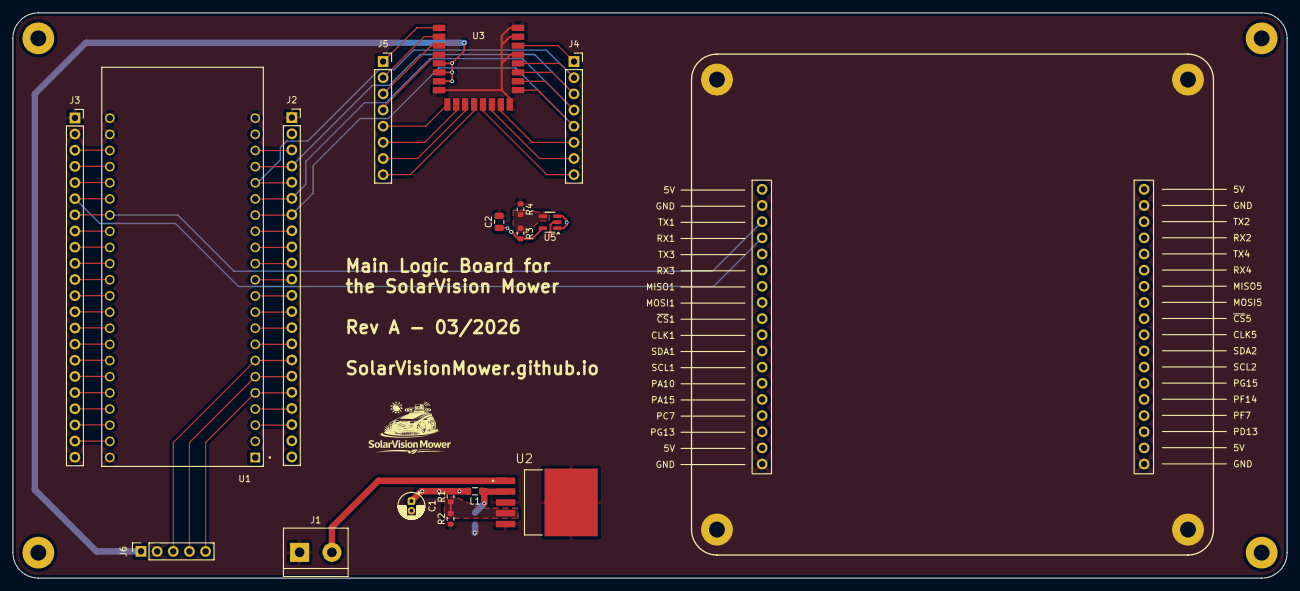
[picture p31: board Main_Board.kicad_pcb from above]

Board: 2 copper layers, 200.3 x 88.8 mm, 19 parts (1 on the bottom side), 56 nets.

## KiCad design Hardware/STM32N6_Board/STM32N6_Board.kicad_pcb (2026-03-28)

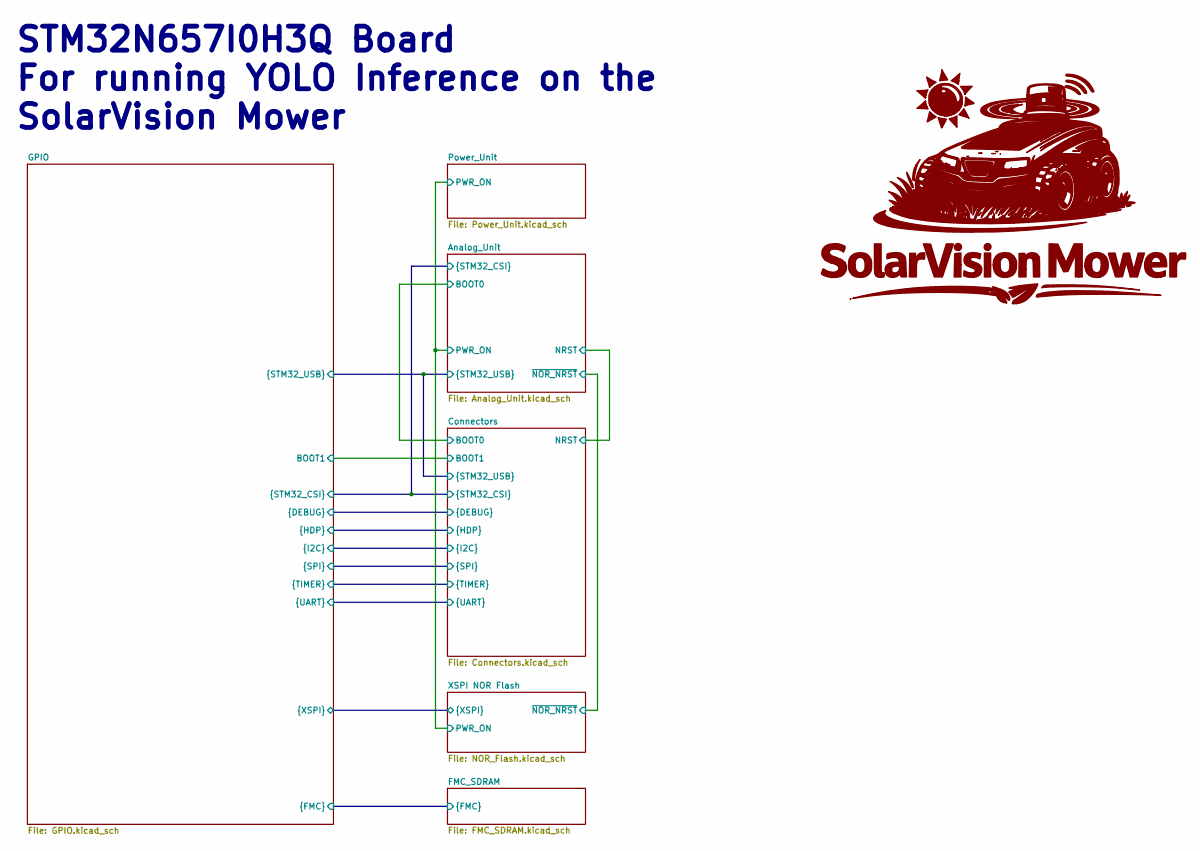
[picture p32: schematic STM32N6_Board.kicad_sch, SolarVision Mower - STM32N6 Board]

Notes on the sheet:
STM32N657I0H3Q Board For running YOLO Inference on the SolarVision Mower

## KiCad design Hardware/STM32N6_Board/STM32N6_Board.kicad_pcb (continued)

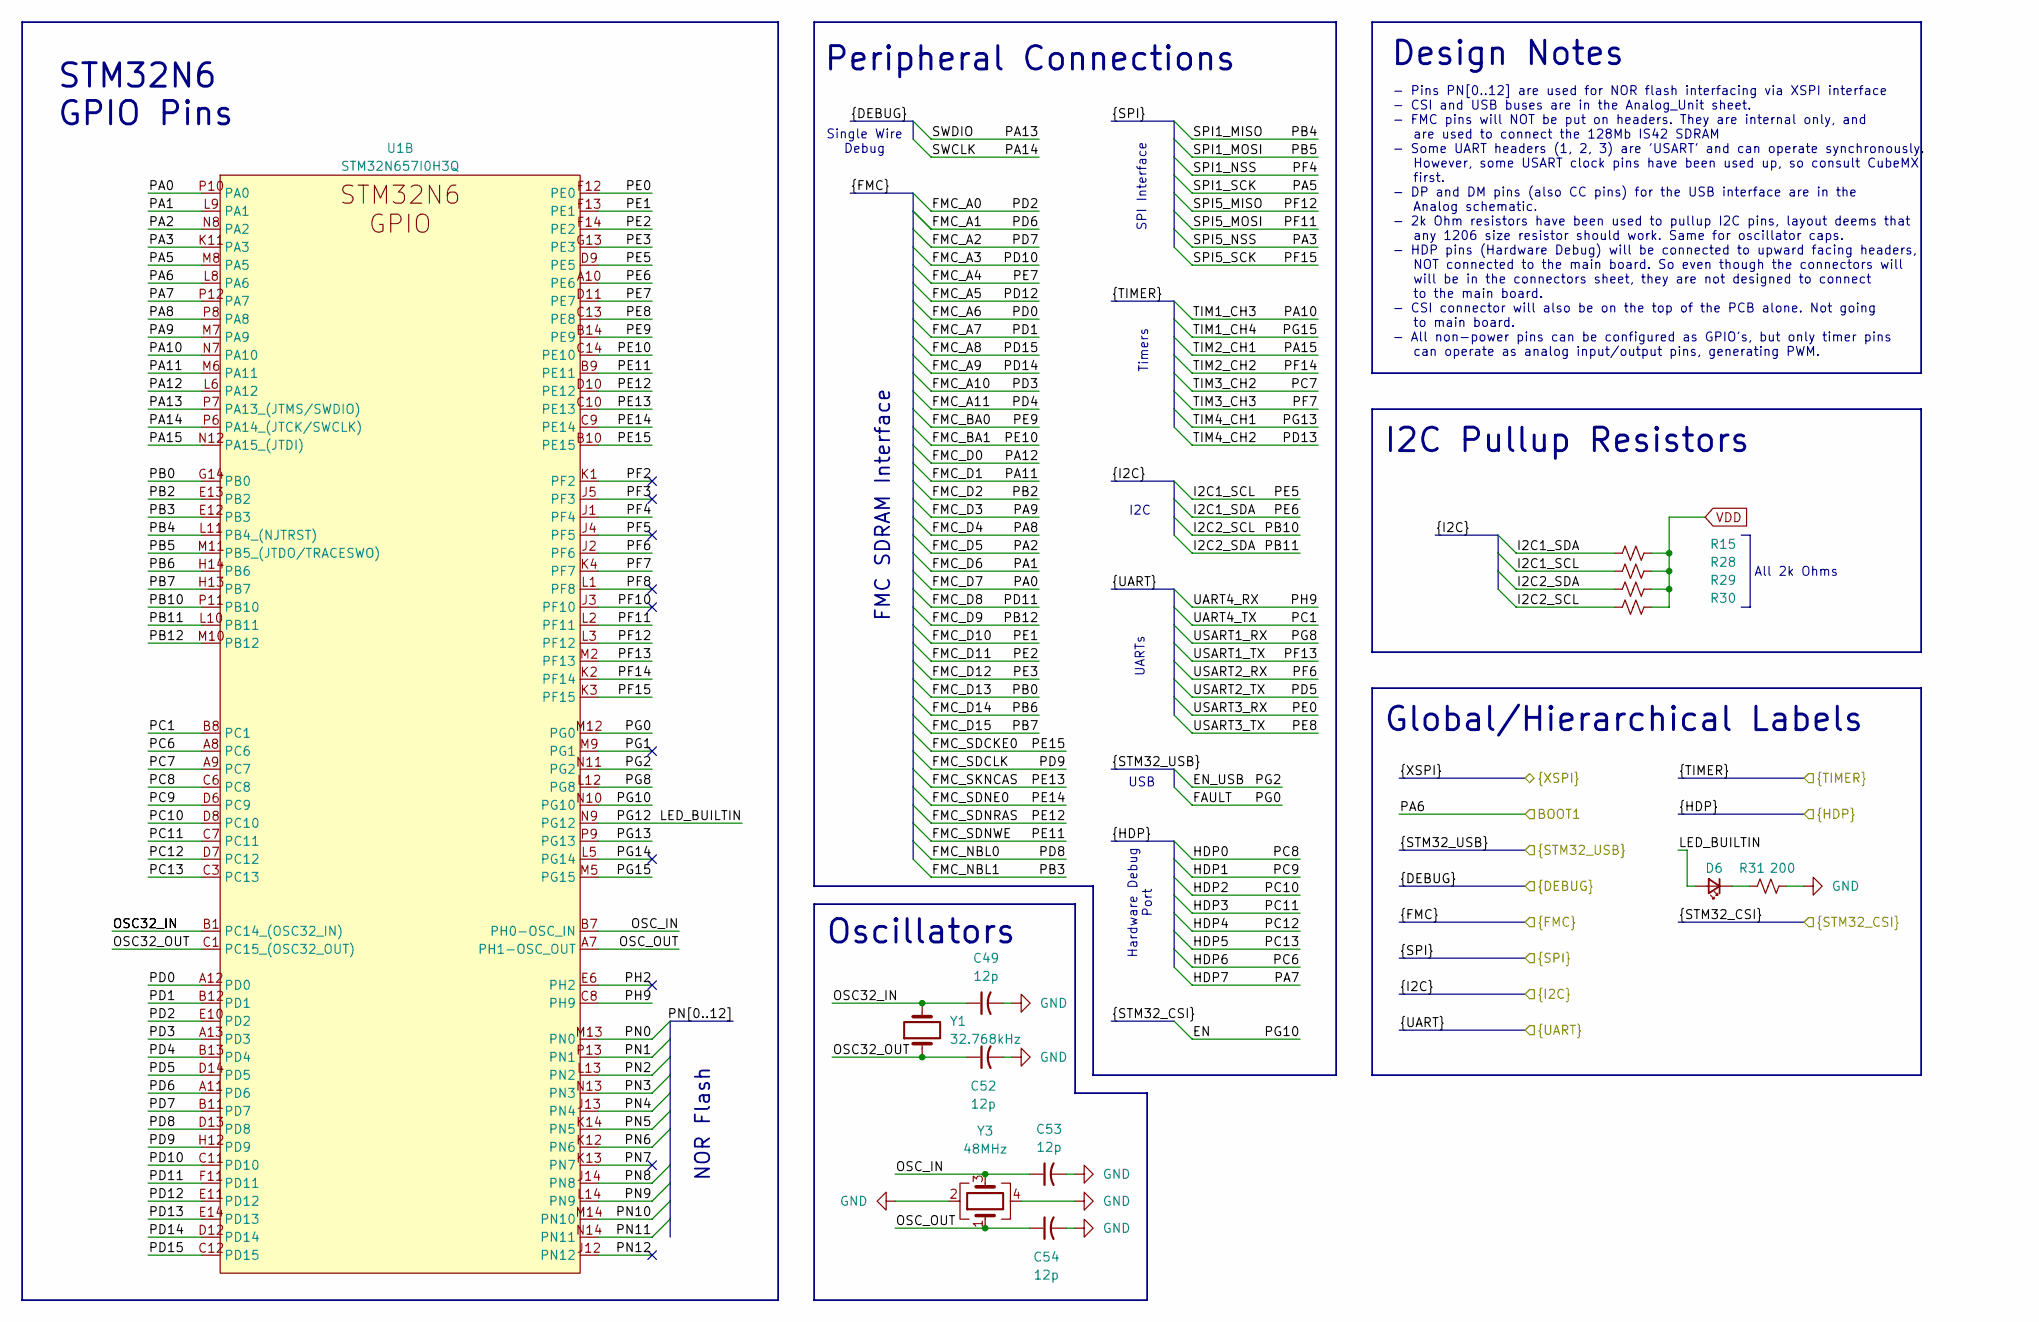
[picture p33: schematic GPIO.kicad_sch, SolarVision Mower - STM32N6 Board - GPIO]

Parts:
C49, C52, C53, C54: 12p; C_0402_1005Metric_Pad0.74x0.62mm_HandSolder
D6: LED_Small; LED_0603_1608Metric_Pad1.05x0.95mm_HandSolder
R15, R28, R29, R30: 2k; R_0402_1005Metric
R31: 200; R_0402_1005Metric
U1: STM32N657I0H3Q; STM32N657I0H3Q_VFBGA178_14x14
Y1: 32.768kHz; 32kHz_SC-20S_2Pin_2.05x1.2mm
Y3: 48MHz; 48MHz_Q22FA12800150_4Pin_2.0z1.6mm

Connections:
/Analog_Unit/EN: U1.N10 (PG10); also elsewhere on the board
/Analog_Unit/EN_USB: U1.N11 (PG2); also elsewhere on the board
/Analog_Unit/FAULT: U1.M12 (PG0); also elsewhere on the board
/Connectors/BOOT1: U1.L8 (PA6); also elsewhere on the board
/Connectors/HDP0: U1.C6 (PC8); also elsewhere on the board
/Connectors/HDP1: U1.D6 (PC9); also elsewhere on the board
/Connectors/HDP2: U1.D8 (PC10); also elsewhere on the board
/Connectors/HDP3: U1.C7 (PC11); also elsewhere on the board
/Connectors/HDP4: U1.D7 (PC12); also elsewhere on the board
/Connectors/HDP5: U1.C3 (PC13); also elsewhere on the board
/Connectors/HDP6: U1.A8 (PC6); also elsewhere on the board
/Connectors/HDP7: U1.P12 (PA7); also elsewhere on the board
/Connectors/I2C1_SCL: R28.1, U1.D9 (PE5); also elsewhere on the board
/Connectors/I2C1_SDA: R15.1, U1.A10 (PE6); also elsewhere on the board
/Connectors/I2C2_SCL: R30.1, U1.P11 (PB10); also elsewhere on the board
/Connectors/I2C2_SDA: R29.1, U1.L10 (PB11); also elsewhere on the board
/Connectors/SPI1_MISO: U1.L11 (PB4_(NJTRST)); also elsewhere on the board
/Connectors/SPI1_MOSI: U1.M11 (PB5_(JTDO/TRACESWO)); also elsewhere on the board
/Connectors/SPI1_NSS: U1.J1 (PF4); also elsewhere on the board
/Connectors/SPI1_SCK: U1.M8 (PA5); also elsewhere on the board
/Connectors/SPI5_MISO: U1.L3 (PF12); also elsewhere on the board
/Connectors/SPI5_MOSI: U1.L2 (PF11); also elsewhere on the board
/Connectors/SPI5_NSS: U1.K11 (PA3); also elsewhere on the board
/Connectors/SPI5_SCK: U1.K3 (PF15); also elsewhere on the board
/Connectors/SWCLK: U1.P6 (PA14_(JTCK/SWCLK)); also elsewhere on the board
/Connectors/SWDIO: U1.P7 (PA13_(JTMS/SWDIO)); also elsewhere on the board
/Connectors/TIM1_CH3: U1.N7 (PA10); also elsewhere on the board
/Connectors/TIM1_CH4: U1.M5 (PG15); also elsewhere on the board
/Connectors/TIM2_CH1: U1.N12 (PA15_(JTDI)); also elsewhere on the board
/Connectors/TIM2_CH2: U1.K2 (PF14); also elsewhere on the board
/Connectors/TIM3_CH2: U1.A9 (PC7); also elsewhere on the board
/Connectors/TIM3_CH3: U1.K4 (PF7); also elsewhere on the board
/Connectors/TIM4_CH1: U1.P9 (PG13); also elsewhere on the board
/Connectors/TIM4_CH2: U1.E14 (PD13); also elsewhere on the board
/Connectors/UART4_RX: U1.C8 (PH9); also elsewhere on the board
/Connectors/UART4_TX: U1.B8 (PC1); also elsewhere on the board
/Connectors/USART1_RX: U1.L12 (PG8); also elsewhere on the board
/Connectors/USART1_TX: U1.M2 (PF13); also elsewhere on the board
/Connectors/USART2_RX: U1.J2 (PF6); also elsewhere on the board
/Connectors/USART2_TX: U1.D14 (PD5); also elsewhere on the board
/Connectors/USART3_RX: U1.F12 (PE0); also elsewhere on the board
/Connectors/USART3_TX: U1.C13 (PE8); also elsewhere on the board
/FMC_SDRAM/FMC_A0: U1.E10 (PD2); also elsewhere on the board
/FMC_SDRAM/FMC_A1: U1.A11 (PD6); also elsewhere on the board
/FMC_SDRAM/FMC_A2: U1.B11 (PD7); also elsewhere on the board
/FMC_SDRAM/FMC_A3: U1.C11 (PD10); also elsewhere on the board
/FMC_SDRAM/FMC_A4: U1.D11 (PE7); also elsewhere on the board
/FMC_SDRAM/FMC_A5: U1.E11 (PD12); also elsewhere on the board
/FMC_SDRAM/FMC_A6: U1.A12 (PD0); also elsewhere on the board
/FMC_SDRAM/FMC_A7: U1.B12 (PD1); also elsewhere on the board
/FMC_SDRAM/FMC_A8: U1.C12 (PD15); also elsewhere on the board
/FMC_SDRAM/FMC_A9: U1.D12 (PD14); also elsewhere on the board
/FMC_SDRAM/FMC_A10: U1.A13 (PD3); also elsewhere on the board
/FMC_SDRAM/FMC_A11: U1.B13 (PD4); also elsewhere on the board
/FMC_SDRAM/FMC_BA0: U1.B14 (PE9); also elsewhere on the board
/FMC_SDRAM/FMC_BA1: U1.C14 (PE10); also elsewhere on the board
/FMC_SDRAM/FMC_D0: U1.L6 (PA12); also elsewhere on the board
/FMC_SDRAM/FMC_D1: U1.M6 (PA11); also elsewhere on the board
/FMC_SDRAM/FMC_D2: U1.E13 (PB2); also elsewhere on the board
/FMC_SDRAM/FMC_D3: U1.M7 (PA9); also elsewhere on the board
/FMC_SDRAM/FMC_D4: U1.P8 (PA8); also elsewhere on the board
/FMC_SDRAM/FMC_D5: U1.N8 (PA2); also elsewhere on the board
/FMC_SDRAM/FMC_D6: U1.L9 (PA1); also elsewhere on the board
/FMC_SDRAM/FMC_D7: U1.P10 (PA0); also elsewhere on the board
/FMC_SDRAM/FMC_D8: U1.F11 (PD11); also elsewhere on the board
/FMC_SDRAM/FMC_D9: U1.M10 (PB12); also elsewhere on the board
/FMC_SDRAM/FMC_D10: U1.F13 (PE1); also elsewhere on the board
/FMC_SDRAM/FMC_D11: U1.F14 (PE2); also elsewhere on the board
/FMC_SDRAM/FMC_D12: U1.G13 (PE3); also elsewhere on the board
/FMC_SDRAM/FMC_D13: U1.G14 (PB0); also elsewhere on the board
/FMC_SDRAM/FMC_D14: U1.H14 (PB6); also elsewhere on the board
/FMC_SDRAM/FMC_D15: U1.H13 (PB7); also elsewhere on the board
/FMC_SDRAM/FMC_NBL0: U1.D13 (PD8); also elsewhere on the board
/FMC_SDRAM/FMC_NBL1: U1.E12 (PB3); also elsewhere on the board
/FMC_SDRAM/FMC_SDCKE0: U1.B10 (PE15); also elsewhere on the board
/FMC_SDRAM/FMC_SDCLK: U1.H12 (PD9); also elsewhere on the board
/FMC_SDRAM/FMC_SDNE0: U1.C9 (PE14); also elsewhere on the board
/FMC_SDRAM/FMC_SDNRAS: U1.D10 (PE12); also elsewhere on the board
/FMC_SDRAM/FMC_SDNWE: U1.B9 (PE11); also elsewhere on the board
/FMC_SDRAM/FMC_SKNCAS: U1.C10 (PE13); also elsewhere on the board
/GPIO/LED_BUILTIN: D6.2 (A), U1.N9 (PG12)
/GPIO/OSC32_IN: C49.1, U1.B1 (PC14_(OSC32_IN)), Y1.2
/GPIO/OSC32_OUT: C52.1, U1.C1 (PC15_(OSC32_OUT)), Y1.1
/GPIO/OSC_IN: C53.1, U1.B7 (PH0-OSC_IN), Y3.3
/GPIO/OSC_OUT: C54.1, U1.A7 (PH1-OSC_OUT), Y3.1
/GPIO/PF2: U1.K1 (PF2)
/GPIO/PF3: U1.J5 (PF3)
/GPIO/PF5: U1.J4 (PF5)
/GPIO/PF8: U1.L1 (PF8)
/GPIO/PF10: U1.J3 (PF10)
/GPIO/PG1: U1.M9 (PG1)
/GPIO/PG14: U1.L5 (PG14)
/GPIO/PH2: U1.E6 (PH2)
/GPIO/PN0: U1.M13 (PN0); also elsewhere on the board
/GPIO/PN1: U1.P13 (PN1); also elsewhere on the board
/GPIO/PN2: U1.L13 (PN2); also elsewhere on the board
/GPIO/PN3: U1.N13 (PN3); also elsewhere on the board
/GPIO/PN4: U1.J13 (PN4); also elsewhere on the board
/GPIO/PN5: U1.K14 (PN5); also elsewhere on the board
/GPIO/PN6: U1.K12 (PN6); also elsewhere on the board
/GPIO/PN7: U1.K13 (PN7)
/GPIO/PN8: U1.J14 (PN8); also elsewhere on the board
/GPIO/PN9: U1.L14 (PN9); also elsewhere on the board
/GPIO/PN10: U1.M14 (PN10); also elsewhere on the board
/GPIO/PN11: U1.N14 (PN11); also elsewhere on the board
/GPIO/PN12: U1.J12 (PN12)
GND: C49.2, C52.2, C53.2, C54.2, R31.2, Y3.2, Y3.4; also elsewhere on the board
unnamed: D6.1 (K), R31.1
VDD: R15.2, R28.2, R29.2, R30.2; also elsewhere on the board

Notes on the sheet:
I2C
Global/Hierarchical Labels
Timers
FMC SDRAM Interface
- Pins PN[0..12] are used for NOR flash interfacing via XSPI interface - CSI and USB buses are in the Analog_Unit sheet. - FMC pins will NOT be put on headers. They are internal only, and are used to connect the 128Mb IS42 SDRAM - Some UART headers (1, 2, 3) are 'USART' and can operate synchronousl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
STM32N6 GPIO Pins
I2C Pullup Resistors
UARTs
Peripheral Connections
Oscillators
USB
Hardware Debug Port
NOR Flash
All 2k Ohms
Single Wire Debug
SPI Interface
Design Notes

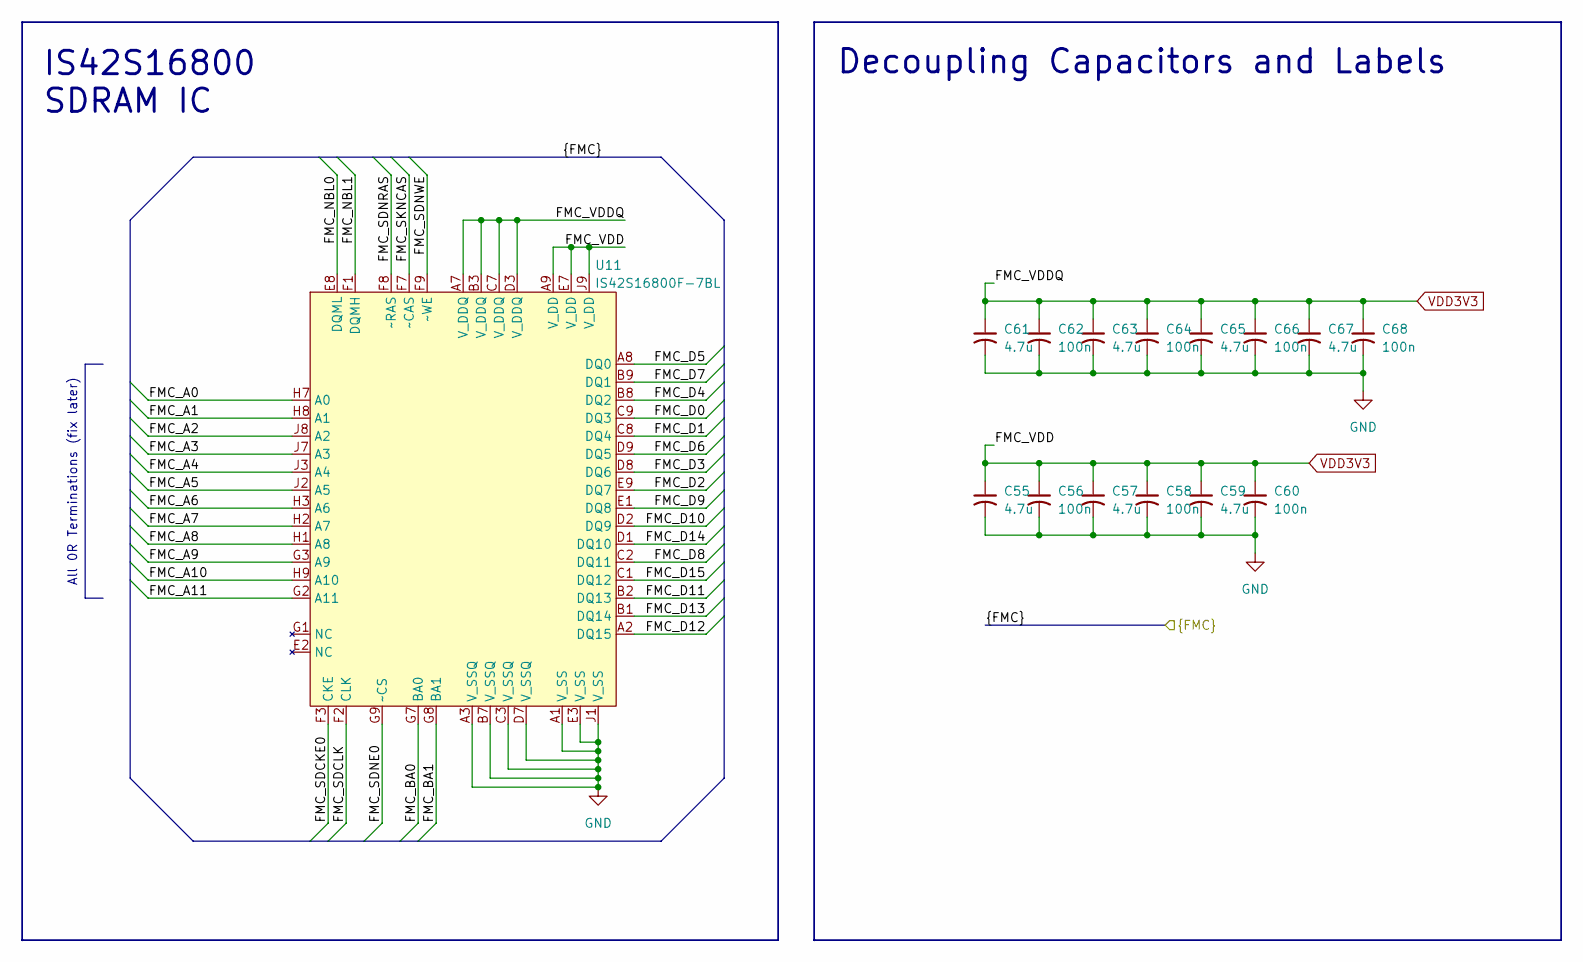
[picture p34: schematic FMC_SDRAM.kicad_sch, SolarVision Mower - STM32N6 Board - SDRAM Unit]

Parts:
C55, C57, C59, C61, C63, C65, C67: 4.7u; C_0402_1005Metric
C56, C58, C60, C62, C64, C66, C68: 100n; C_0402_1005Metric
U11: IS42S16800F-7BL; IS42S16800F-7BL_BGA54C80P9X9_800X800X120

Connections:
/FMC_SDRAM/FMC_A0: U11.H7 (A0); also elsewhere on the board
/FMC_SDRAM/FMC_A1: U11.H8 (A1); also elsewhere on the board
/FMC_SDRAM/FMC_A2: U11.J8 (A2); also elsewhere on the board
/FMC_SDRAM/FMC_A3: U11.J7 (A3); also elsewhere on the board
/FMC_SDRAM/FMC_A4: U11.J3 (A4); also elsewhere on the board
/FMC_SDRAM/FMC_A5: U11.J2 (A5); also elsewhere on the board
/FMC_SDRAM/FMC_A6: U11.H3 (A6); also elsewhere on the board
/FMC_SDRAM/FMC_A7: U11.H2 (A7); also elsewhere on the board
/FMC_SDRAM/FMC_A8: U11.H1 (A8); also elsewhere on the board
/FMC_SDRAM/FMC_A9: U11.G3 (A9); also elsewhere on the board
/FMC_SDRAM/FMC_A10: U11.H9 (A10); also elsewhere on the board
/FMC_SDRAM/FMC_A11: U11.G2 (A11); also elsewhere on the board
/FMC_SDRAM/FMC_BA0: U11.G7 (BA0); also elsewhere on the board
/FMC_SDRAM/FMC_BA1: U11.G8 (BA1); also elsewhere on the board
/FMC_SDRAM/FMC_D0: U11.C9 (DQ3); also elsewhere on the board
/FMC_SDRAM/FMC_D1: U11.C8 (DQ4); also elsewhere on the board
/FMC_SDRAM/FMC_D2: U11.E9 (DQ7); also elsewhere on the board
/FMC_SDRAM/FMC_D3: U11.D8 (DQ6); also elsewhere on the board
/FMC_SDRAM/FMC_D4: U11.B8 (DQ2); also elsewhere on the board
/FMC_SDRAM/FMC_D5: U11.A8 (DQ0); also elsewhere on the board
/FMC_SDRAM/FMC_D6: U11.D9 (DQ5); also elsewhere on the board
/FMC_SDRAM/FMC_D7: U11.B9 (DQ1); also elsewhere on the board
/FMC_SDRAM/FMC_D8: U11.C2 (DQ11); also elsewhere on the board
/FMC_SDRAM/FMC_D9: U11.E1 (DQ8); also elsewhere on the board
/FMC_SDRAM/FMC_D10: U11.D2 (DQ9); also elsewhere on the board
/FMC_SDRAM/FMC_D11: U11.B2 (DQ13); also elsewhere on the board
/FMC_SDRAM/FMC_D12: U11.A2 (DQ15); also elsewhere on the board
/FMC_SDRAM/FMC_D13: U11.B1 (DQ14); also elsewhere on the board
/FMC_SDRAM/FMC_D14: U11.D1 (DQ10); also elsewhere on the board
/FMC_SDRAM/FMC_D15: U11.C1 (DQ12); also elsewhere on the board
/FMC_SDRAM/FMC_NBL0: U11.E8 (DQML); also elsewhere on the board
/FMC_SDRAM/FMC_NBL1: U11.F1 (DQMH); also elsewhere on the board
/FMC_SDRAM/FMC_SDCKE0: U11.F3 (CKE); also elsewhere on the board
/FMC_SDRAM/FMC_SDCLK: U11.F2 (CLK); also elsewhere on the board
/FMC_SDRAM/FMC_SDNE0: U11.G9 (~CS); also elsewhere on the board
/FMC_SDRAM/FMC_SDNRAS: U11.F8 (~RAS); also elsewhere on the board
/FMC_SDRAM/FMC_SDNWE: U11.F9 (~WE); also elsewhere on the board
/FMC_SDRAM/FMC_SKNCAS: U11.F7 (~CAS); also elsewhere on the board
GND: C55.2, C56.2, C57.2, C58.2, C59.2, C60.2, C61.2, C62.2, C63.2, C64.2, C65.2, C66.2, C67.2, C68.2, U11.A1 (V_SS), U11.A3 (V_SSQ), U11.B7 (V_SSQ), U11.C3 (V_SSQ), U11.D7 (V_SSQ), U11.E3 (V_SS), U11.J1 (V_SS); also elsewhere on the board
VDD3V3: C55.1, C56.1, C57.1, C58.1, C59.1, C60.1, C61.1, C62.1, C63.1, C64.1, C65.1, C66.1, C67.1, C68.1, U11.A7 (V_DDQ), U11.A9 (V_DD), U11.B3 (V_DDQ), U11.C7 (V_DDQ), U11.D3 (V_DDQ), U11.E7 (V_DD), U11.J9 (V_DD); also elsewhere on the board

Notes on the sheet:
All 0R Terminations (fix later)
IS42S16800 SDRAM IC
Decoupling Capacitors and Labels

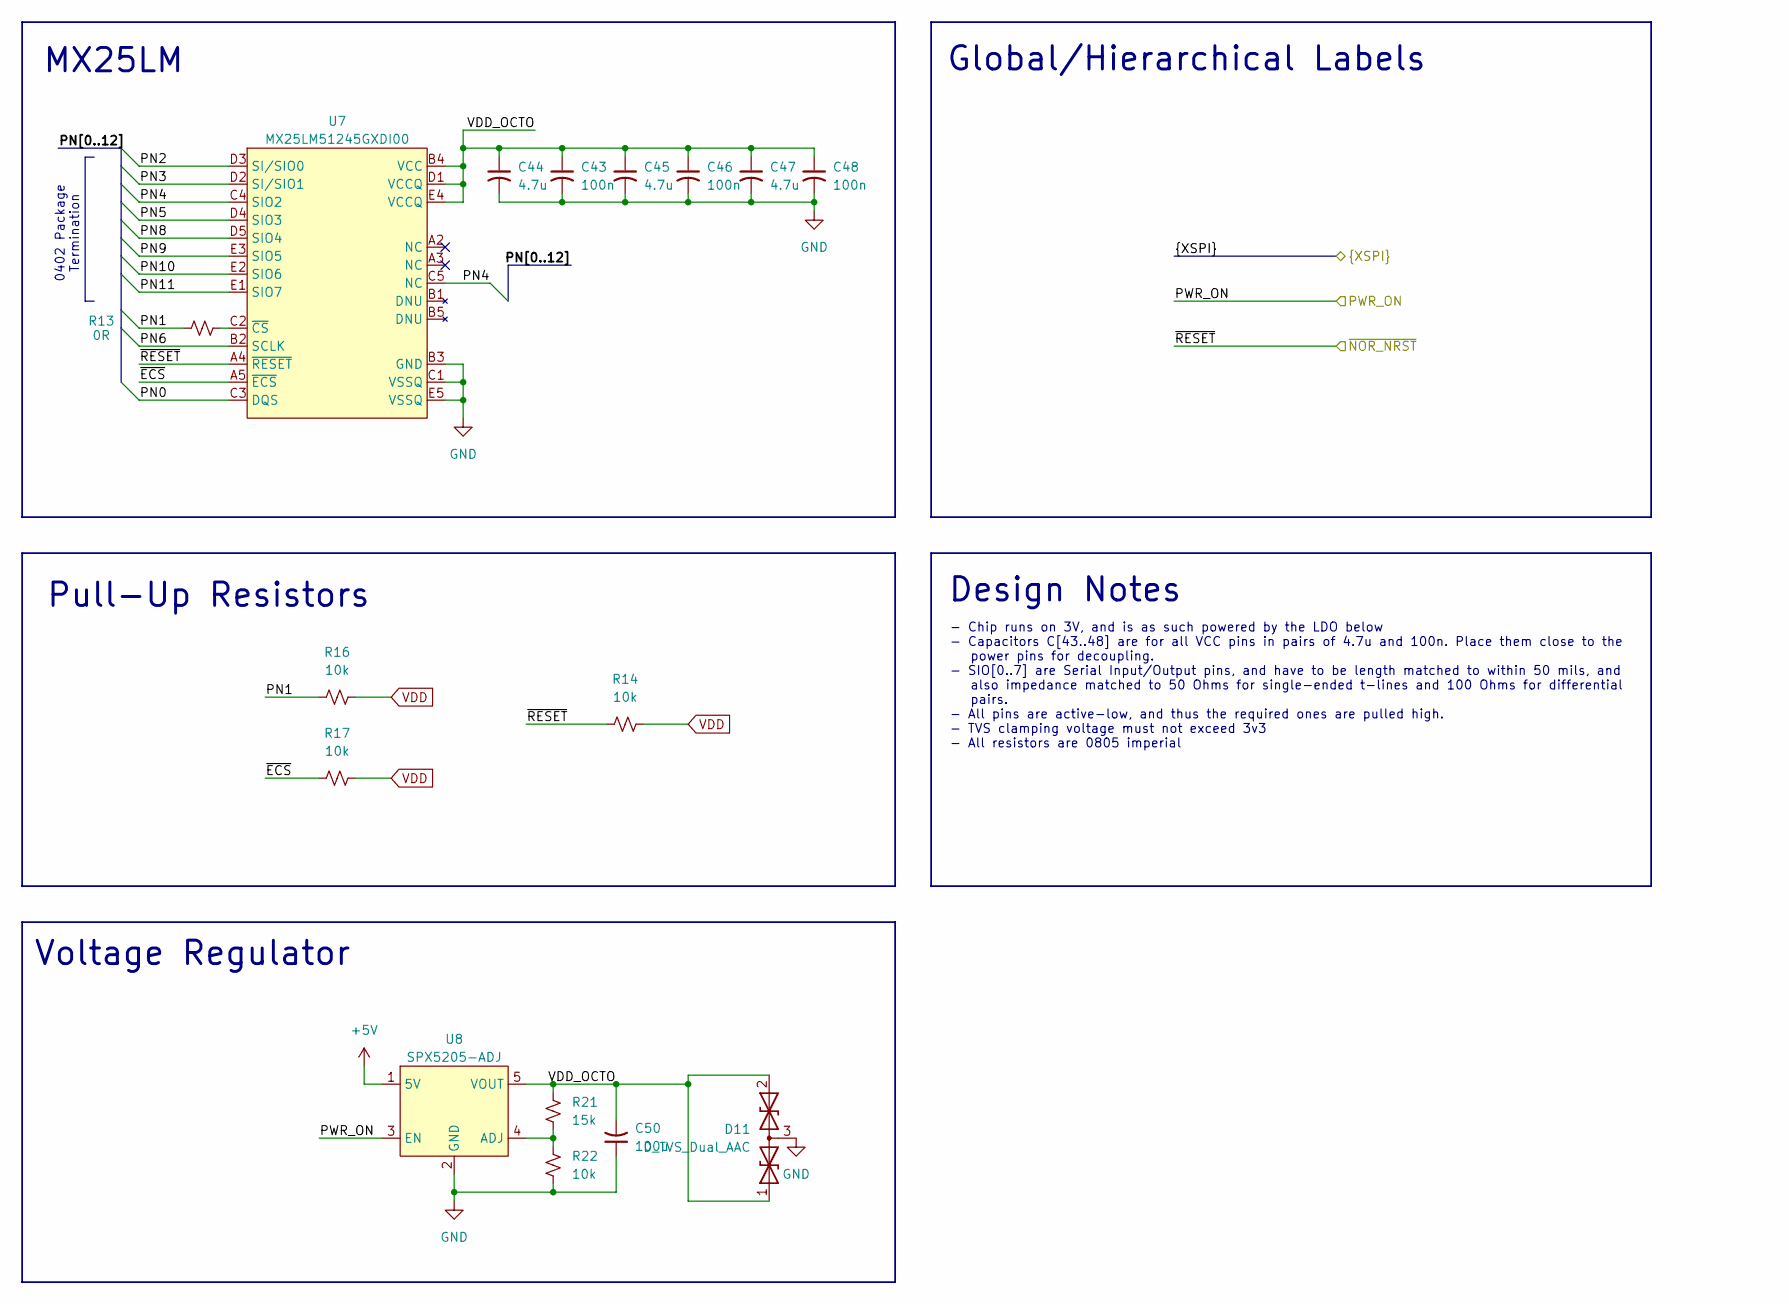
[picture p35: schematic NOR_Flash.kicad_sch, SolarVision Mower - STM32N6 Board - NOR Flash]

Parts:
C43, C46, C48: 100n; C_0402_1005Metric
C44, C45, C47: 4.7u; C_0402_1005Metric
C50: 100u; C_0805_2012Metric_Pad1.18x1.45mm_HandSolder
D11: D_TVS_Dual_AAC; SOT-723
R13: 0R; R_0402_1005Metric
R14, R16, R17: 10k; R_0402_1005Metric
R21: 15k; R_0805_2012Metric_Pad1.20x1.40mm_HandSolder
R22: 10k; R_0805_2012Metric_Pad1.20x1.40mm_HandSolder
U7: MX25LM51245GXDI00; MX25LM51245GXD100_BGA24C100P5X5_600X800X120
U8: SPX5205-ADJ; SOT-23-5

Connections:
+5V: U8.1 (5V); also elsewhere on the board
/Analog_Unit/NRST: R14.1, U7.A4 (~RESET); also elsewhere on the board
/Analog_Unit/PWR_ON: U8.3 (EN); also elsewhere on the board
/GPIO/PN0: U7.C3 (DQS); also elsewhere on the board
/GPIO/PN1: R13.1, R16.1; also elsewhere on the board
/GPIO/PN2: U7.D3 (SI/SIO0); also elsewhere on the board
/GPIO/PN3: U7.D2 (SI/SIO1); also elsewhere on the board
/GPIO/PN4: U7.C4 (SIO2), U7.C5 (NC); also elsewhere on the board
/GPIO/PN5: U7.D4 (SIO3); also elsewhere on the board
/GPIO/PN6: U7.B2 (SCLK); also elsewhere on the board
/GPIO/PN8: U7.D5 (SIO4); also elsewhere on the board
/GPIO/PN9: U7.E3 (SIO5); also elsewhere on the board
/GPIO/PN10: U7.E2 (SIO6); also elsewhere on the board
/GPIO/PN11: U7.E1 (SIO7); also elsewhere on the board
/XSPI NOR Flash/VDD_OCTO: C43.1, C44.1, C45.1, C46.1, C47.1, C48.1, C50.2, D11.1 (A1), D11.2 (A2), R21.1, U7.B4 (VCC), U7.D1 (VCCQ), U7.E4 (VCCQ), U8.5 (VOUT)
/XSPI NOR Flash/~ECS: R17.1, U7.A5 (~ECS)
GND: C43.2, C44.2, C45.2, C46.2, C47.2, C48.2, C50.1, D11.3 (common), R22.2, U7.B3 (GND), U7.C1 (VSSQ), U7.E5 (VSSQ), U8.2 (GND); also elsewhere on the board
unnamed: R13.2, U7.C2 (~CS)
unnamed: R21.2, R22.1, U8.4 (ADJ)
VDD: R14.2, R16.2, R17.2; also elsewhere on the board

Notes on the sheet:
- Chip runs on 3V, and is as such powered by the LDO below - Capacitors C[43..48] are for all VCC pins in pairs of 4.7u and 100n. Place them close to the power pins for decoupling. - SIO[0..7] are Serial Input/Output pins, and have to be length matched to within 50 mils, and also impedance matched 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
MX25LM
Global/Hierarchical Labels
Pull-Up Resistors
Voltage Regulator
0402 Package Termination
Design Notes

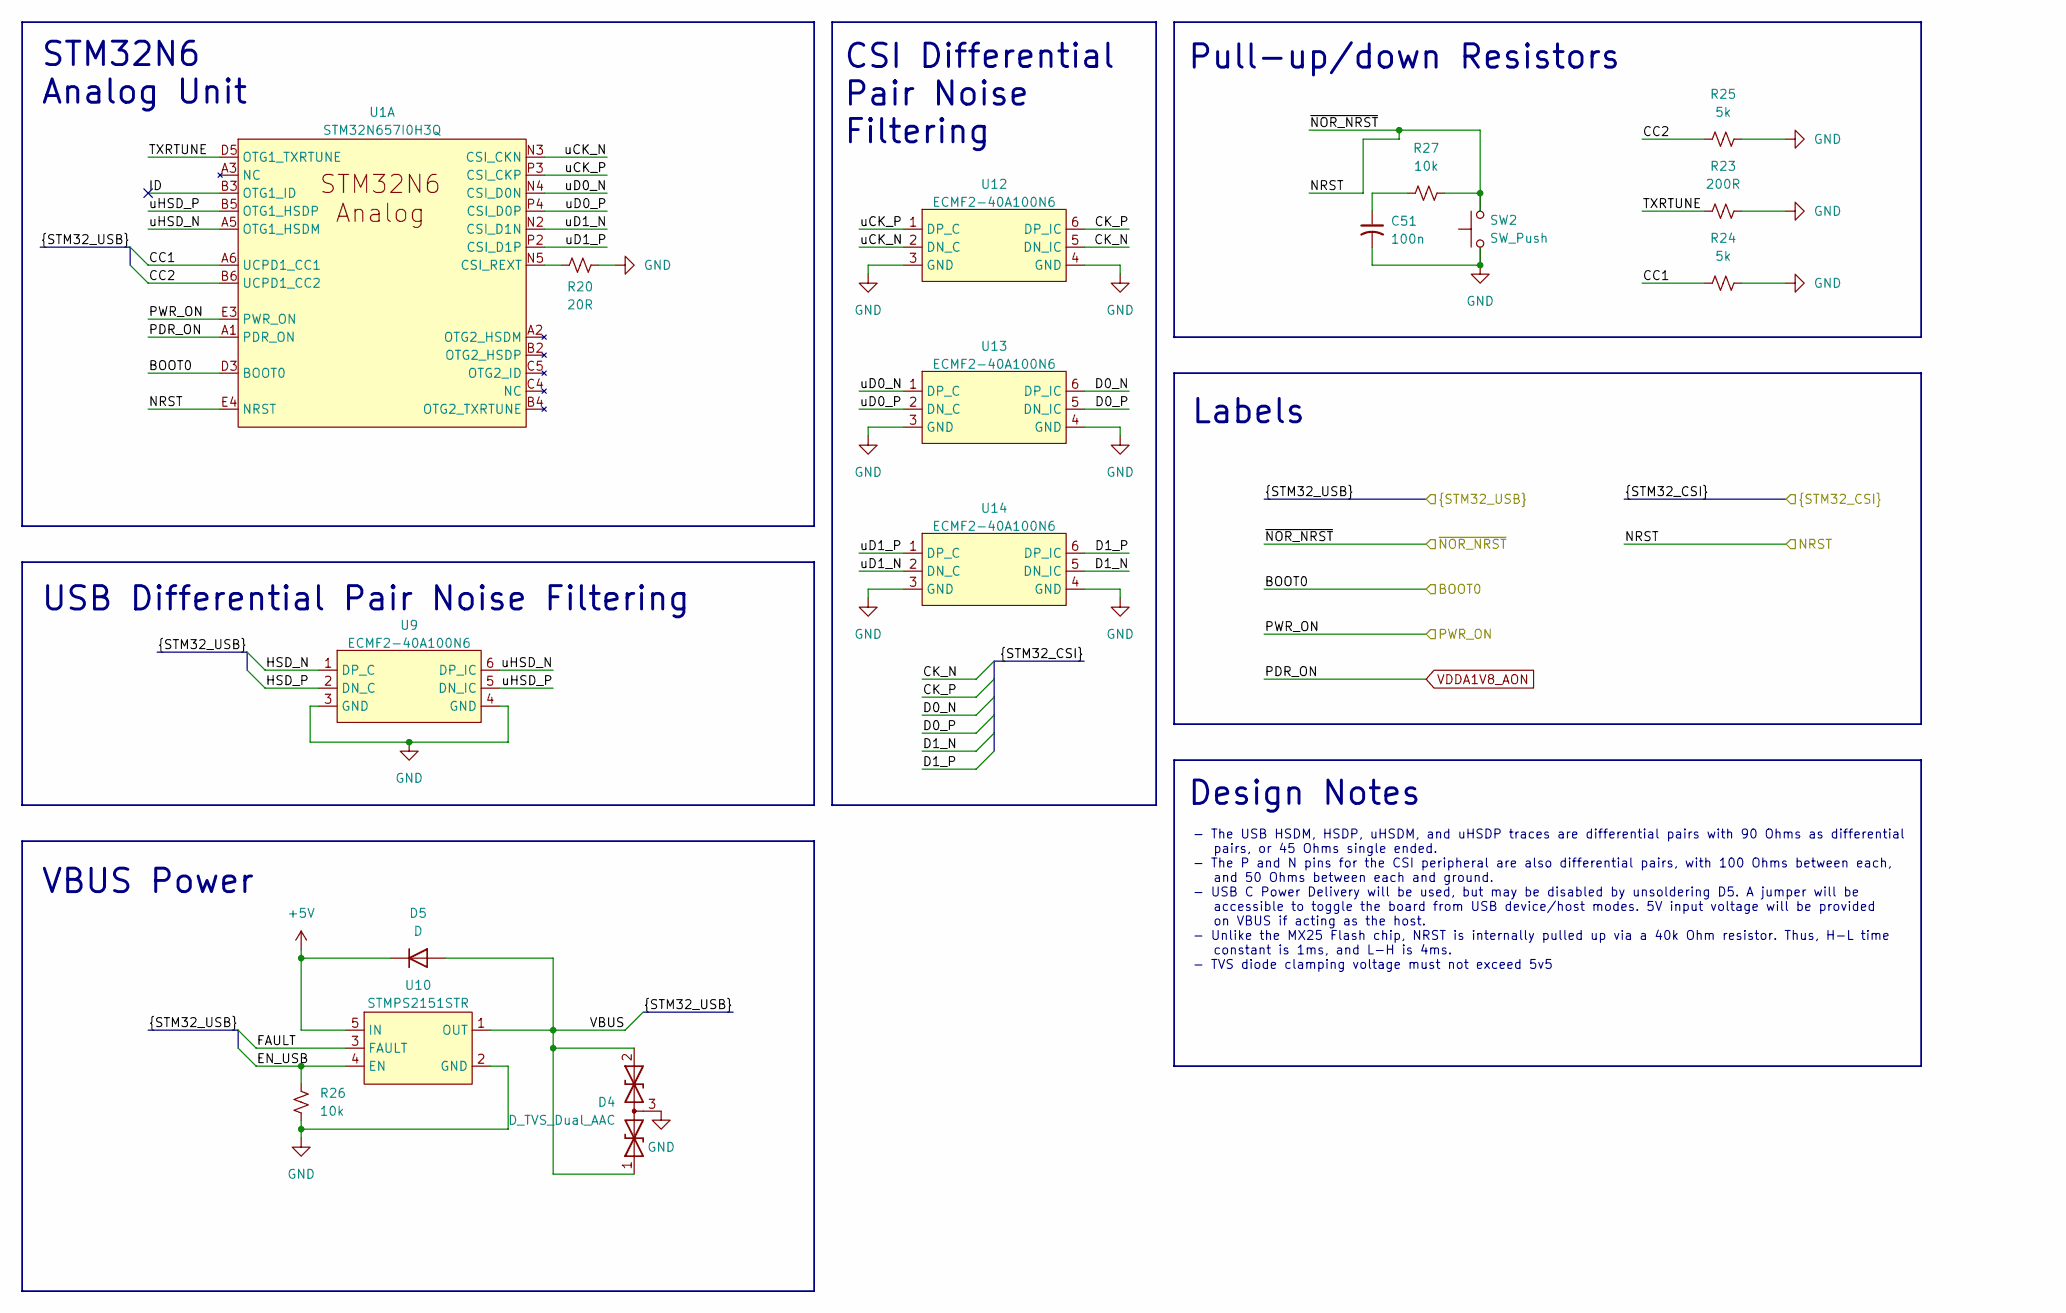
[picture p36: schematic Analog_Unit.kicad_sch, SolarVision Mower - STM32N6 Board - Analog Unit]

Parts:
C51: 100n; C_0805_2012Metric_Pad1.18x1.45mm_HandSolder
D4: D_TVS_Dual_AAC; SOT-723
D5: D; LED_0805_2012Metric_Pad1.15x1.40mm_HandSolder
R20: 20R; R_0402_1005Metric
R23: 200R; R_0402_1005Metric
R24, R25: 5k; R_0402_1005Metric
R26: 10k; R_0402_1005Metric
R27: 10k; R_0805_2012Metric_Pad1.20x1.40mm_HandSolder
SW2: SW_Push; SW_SPST_Omron_B3FS-101xP
U1: STM32N657I0H3Q; STM32N657I0H3Q_VFBGA178_14x14
U9, U12, U13, U14: ECMF2-40A100N6; ST_UQFN-6L_1.5x1.7mm_P0.5mm
U10: STMPS2151STR; SOT-23-5

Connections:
+5V: D5.1 (K), U10.5 (IN); also elsewhere on the board
/Analog_Unit/BOOT0: U1.D3 (BOOT0); also elsewhere on the board
/Analog_Unit/CC1: R24.1, U1.A6 (UCPD1_CC1); also elsewhere on the board
/Analog_Unit/CC2: R25.1, U1.B6 (UCPD1_CC2); also elsewhere on the board
/Analog_Unit/CK_N: U12.5 (DN_IC); also elsewhere on the board
/Analog_Unit/CK_P: U12.6 (DP_IC); also elsewhere on the board
/Analog_Unit/D0_N: U13.6 (DP_IC); also elsewhere on the board
/Analog_Unit/D0_P: U13.5 (DN_IC); also elsewhere on the board
/Analog_Unit/D1_N: U14.5 (DN_IC); also elsewhere on the board
/Analog_Unit/D1_P: U14.6 (DP_IC); also elsewhere on the board
/Analog_Unit/EN_USB: R26.2, U10.4 (EN); also elsewhere on the board
/Analog_Unit/FAULT: U10.3 (FAULT); also elsewhere on the board
/Analog_Unit/HSD_N: U9.1 (DP_C); also elsewhere on the board
/Analog_Unit/HSD_P: U9.2 (DN_C); also elsewhere on the board
/Analog_Unit/ID: U1.B3 (OTG1_ID)
/Analog_Unit/NRST: R27.2, SW2.2, U1.E4 (NRST); also elsewhere on the board
/Analog_Unit/PWR_ON: U1.E3 (PWR_ON); also elsewhere on the board
/Analog_Unit/TXRTUNE: R23.1, U1.D5 (OTG1_TXRTUNE)
/Analog_Unit/VBUS: D4.1 (A1), D4.2 (A2), D5.2 (A), U10.1 (OUT); also elsewhere on the board
/Analog_Unit/uCK_N: U1.N3 (CSI_CKN), U12.2 (DN_C)
/Analog_Unit/uCK_P: U1.P3 (CSI_CKP), U12.1 (DP_C)
/Analog_Unit/uD0_N: U1.N4 (CSI_D0N), U13.1 (DP_C)
/Analog_Unit/uD0_P: U1.P4 (CSI_D0P), U13.2 (DN_C)
/Analog_Unit/uD1_N: U1.N2 (CSI_D1N), U14.2 (DN_C)
/Analog_Unit/uD1_P: U1.P2 (CSI_D1P), U14.1 (DP_C)
/Analog_Unit/uHSD_N: U1.A5 (OTG1_HSDM), U9.6 (DP_IC)
/Analog_Unit/uHSD_P: U1.B5 (OTG1_HSDP), U9.5 (DN_IC)
GND: C51.2, D4.3 (common), R20.2, R23.2, R24.2, R25.2, R26.1, SW2.1, U9.3 (GND), U9.4 (GND), U10.2 (GND), U12.3 (GND), U12.4 (GND), U13.3 (GND), U13.4 (GND), U14.3 (GND), U14.4 (GND); also elsewhere on the board
unnamed: C51.1, R27.1
unnamed: R20.1, U1.N5 (CSI_REXT)
VDDA1V8_AON: U1.A1 (PDR_ON); also elsewhere on the board

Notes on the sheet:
VBUS Power
USB Differential Pair Noise Filtering
Design Notes
- The USB HSDM, HSDP, uHSDM, and uHSDP traces are differential pairs with 90 Ohms as differential pairs, or 45 Ohms single ended. - The P and N pins for the CSI peripheral are also differential pairs, with 100 Ohms between each, and 50 Ohms between each and ground. - USB C Power Delivery will be us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
CSI Differential Pair Noise Filtering
Pull-up/down Resistors
STM32N6 Analog Unit
Labels

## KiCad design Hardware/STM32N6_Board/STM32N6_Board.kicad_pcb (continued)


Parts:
C69: 1u; C_0805_2012Metric_Pad1.18x1.45mm_HandSolder
J3: Conn_01x08_Pin; PinHeader_1x08_P2.54mm_Vertical
J4, J5: Conn_01x18_Pin; PinHeader_1x18_P2.54mm_Vertical
J6: Conn_01x05_Pin; PinHeader_1x05_P2.54mm_Vertical
J7: SFW15R-2STE1LF; AMPHENOL_SFW15R-2STE1LF; PARTREV AE
J9: BOOT1; PinHeader_1x03_P2.54mm_Vertical
J10: BOOT0; PinHeader_1x03_P2.54mm_Vertical
J11, J12: Conn_01x18_Socket; PinSocket_1x18_P2.54mm_Vertical
J13: TYPE-C_16PIN_2MD__073_; SHOUHAN_TYPE-C_16PIN_2MD__073_; PARTREV A
R44, R45, R46, R47, R48, R49: 0R; R_0402_1005Metric

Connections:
+5V: J4.1, J4.17, J5.1, J5.17, J11.1, J11.17, J12.1, J12.17; also elsewhere on the board
/Analog_Unit/BOOT0: J10.2; also elsewhere on the board
/Analog_Unit/CC1: J13.A5 (CC1); also elsewhere on the board
/Analog_Unit/CC2: J13.B5 (CC2); also elsewhere on the board
/Analog_Unit/CK_N: R48.1; also elsewhere on the board
/Analog_Unit/CK_P: R49.1; also elsewhere on the board
/Analog_Unit/D0_N: R44.1; also elsewhere on the board
/Analog_Unit/D0_P: R45.1; also elsewhere on the board
/Analog_Unit/D1_N: R46.1; also elsewhere on the board
/Analog_Unit/D1_P: R47.1; also elsewhere on the board
/Analog_Unit/EN: J7.11; also elsewhere on the board
/Analog_Unit/HSD_N: J13.A7 (DN1), J13.B7 (DN2); also elsewhere on the board
/Analog_Unit/HSD_P: J13.A6 (DP1), J13.B6 (DP2); also elsewhere on the board
/Analog_Unit/NRST: J6.4; also elsewhere on the board
/Analog_Unit/VBUS: J13.A4_B9 (VBUS_A), J13.B4_A9 (VBUS_B); also elsewhere on the board
/Connectors/BOOT1: J9.2; also elsewhere on the board
/Connectors/HDP0: J3.1; also elsewhere on the board
/Connectors/HDP1: J3.2; also elsewhere on the board
/Connectors/HDP2: J3.3; also elsewhere on the board
/Connectors/HDP3: J3.4; also elsewhere on the board
/Connectors/HDP4: J3.5; also elsewhere on the board
/Connectors/HDP5: J3.6; also elsewhere on the board
/Connectors/HDP6: J3.7; also elsewhere on the board
/Connectors/HDP7: J3.8; also elsewhere on the board
/Connectors/I2C1_SCL: J5.12, J12.12; also elsewhere on the board
/Connectors/I2C1_SDA: J5.11, J12.11; also elsewhere on the board
/Connectors/I2C2_SCL: J4.12, J7.13, J11.12; also elsewhere on the board
/Connectors/I2C2_SDA: J4.11, J7.14, J11.11; also elsewhere on the board
/Connectors/SPI1_MISO: J5.7, J12.7; also elsewhere on the board
/Connectors/SPI1_MOSI: J5.8, J12.8; also elsewhere on the board
/Connectors/SPI1_NSS: J5.9, J12.9; also elsewhere on the board
/Connectors/SPI1_SCK: J5.10, J12.10; also elsewhere on the board
/Connectors/SPI5_MISO: J4.7, J11.7; also elsewhere on the board
/Connectors/SPI5_MOSI: J4.8, J11.8; also elsewhere on the board
/Connectors/SPI5_NSS: J4.9, J11.9; also elsewhere on the board
/Connectors/SPI5_SCK: J4.10, J11.10; also elsewhere on the board
/Connectors/SWCLK: J6.3; also elsewhere on the board
/Connectors/SWDIO: J6.2; also elsewhere on the board
/Connectors/TIM1_CH3: J5.13, J12.13; also elsewhere on the board
/Connectors/TIM1_CH4: J4.13, J11.13; also elsewhere on the board
/Connectors/TIM2_CH1: J5.14, J12.14; also elsewhere on the board
/Connectors/TIM2_CH2: J4.14, J11.14; also elsewhere on the board
/Connectors/TIM3_CH2: J5.15, J12.15; also elsewhere on the board
/Connectors/TIM3_CH3: J4.15, J11.15; also elsewhere on the board
/Connectors/TIM4_CH1: J5.16, J12.16; also elsewhere on the board
/Connectors/TIM4_CH2: J4.16, J11.16; also elsewhere on the board
/Connectors/UART4_RX: J4.6, J11.6; also elsewhere on the board
/Connectors/UART4_TX: J4.5, J11.5; also elsewhere on the board
/Connectors/USART1_RX: J5.4, J12.4; also elsewhere on the board
/Connectors/USART1_TX: J5.3, J12.3; also elsewhere on the board
/Connectors/USART2_RX: J4.4, J11.4; also elsewhere on the board
/Connectors/USART2_TX: J4.3, J11.3; also elsewhere on the board
/Connectors/USART3_RX: J5.6, J12.6; also elsewhere on the board
/Connectors/USART3_TX: J5.5, J12.5; also elsewhere on the board
GND: C69.2, J4.2, J4.18, J5.2, J5.18, J6.5, J7.1, J7.4, J7.7, J7.10, J7.S1 (SHIELD), J7.S2 (SHIELD__1), J9.3, J10.3, J11.2, J11.18, J12.2, J12.18, J13.A1_B12 (GND_A), J13.B1_A12 (GND_B), J13.SH1 (SHIELD), J13.SH2 (SHIELD), J13.SH3 (SHIELD), J13.SH4 (SHIELD); also elsewhere on the board
unnamed: J7.2, R44.2
unnamed: J7.3, R45.2
unnamed: J7.5, R46.2
unnamed: J7.6, R47.2
unnamed: J7.8, R48.2
unnamed: J7.9, R49.2
VDD: C69.1, J6.1, J7.15, J9.1, J10.1; also elsewhere on the board

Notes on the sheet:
Headers to Main Board
CSI-2 Connector
UART
- I2C1 is sent to main board via header pins, but CSI also uses I2C1. Thus unusable if CSI is in use. - CSI connector and pinout inspiration comes from Raspberry Pi documentation. Specifically camera module 2 and 3 schematics. - 8 Pin hardware debug will most likely not be used, but cannot be disab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
Design Notes
Boot Mode Selection
For Raspberry Pi compatible CSI camera
8-Pin Debug Header
SPI
USB Connector
TIMERS
Labels
I2C
0402 Package Termination
Single Wire Debug and Program


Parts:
C1: 4.7u; C_0402_1005Metric
C3, C4, C5, C35: 15u; C_0402_1005Metric
C7, C8, C13, C14, C15, C16, C17, C18, C19, C21, C22, C30, C31, C32, C33, C34: 100n; C_0402_1005Metric
C9, C10: 10u; C_0402_1005Metric
C11, C12, C20, C23, C24, C25, C26, C27, C28: 1u; C_0402_1005Metric
C29: 1u; C_0805_2012Metric_Pad1.18x1.45mm_HandSolder
C36, C39, C40, C41, C42: 100u; C_0805_2012Metric_Pad1.18x1.45mm_HandSolder
C37: 470p; C_0402_1005Metric
C38: 25u; C_0402_1005Metric
D1: D_Schottky; Schottky_DIOM4325X250N
D2, D3: LED; LED_0603_1608Metric_Pad1.05x0.95mm_HandSolder
D7, D8, D9, D10: D_TVS_Dual_AAC; SOT-723
FB1: 50R@100M; L_1206_3216Metric_Pad1.42x1.75mm_HandSolder
FB2: 70R@100M; L_1206_3216Metric_Pad1.42x1.75mm_HandSolder
J1: Conn_01x02_Pin; PinHeader_1x02_P2.54mm_Vertical
L2: 2.2n; L_1206_3216Metric_Pad1.42x1.75mm_HandSolder
L3: 25u; L_1206_3216Metric_Pad1.42x1.75mm_HandSolder
R1, R4, R6, R10: 7k; R_0805_2012Metric_Pad1.20x1.40mm_HandSolder
R2: 100m; R_0805_2012Metric_Pad1.20x1.40mm_HandSolder
R3, R5, R7: 15k; R_0805_2012Metric_Pad1.20x1.40mm_HandSolder
R8: 17k; R_0805_2012Metric_Pad1.20x1.40mm_HandSolder
R9: 10k; R_0805_2012Metric_Pad1.20x1.40mm_HandSolder
R11: 5k; R_0805_2012Metric_Pad1.20x1.40mm_HandSolder
R12: 3k; R_0805_2012Metric_Pad1.20x1.40mm_HandSolder
R18, R19: 200R; R_0402_1005Metric
U1: STM32N657I0H3Q; STM32N657I0H3Q_VFBGA178_14x14
U2, U3, U4, U5: SPX5205-ADJ; SOT-23-5
U6: MC34064-ADJ-TR; SO-8_3.9x4.9mm_P1.27mm

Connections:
+5V: C36.2, D7.1 (A1), D7.2 (A2), D8.1 (A1), D8.2 (A2), D9.1 (A1), D9.2 (A2), D10.1 (A1), D10.2 (A2), R10.1, U2.1 (5V), U2.3 (EN), U3.1 (5V), U4.1 (5V), U5.1 (5V), U6.6 (VCC); also elsewhere on the board
/Analog_Unit/PWR_ON: U3.3 (EN), U4.3 (EN), U5.3 (EN); also elsewhere on the board
/Power_Unit/Buck_Feedback: R10.2, U6.1 (SWC), U6.7 (IPK), U6.8 (DRC)
/Power_Unit/VDDA1V8PMU: C30.2, FB1.1, U1.E1 (VDDA18PMU)
/Power_Unit/VDDCORE: C3.1, C4.1, C5.1, C23.1, C24.1, C25.1, C26.1, C27.1, C28.1, C35.1, FB2.2, U1.D2 (VFBSMPS), U1.K6 (VDDCORE), U1.K7 (VDDCORE), U1.K8 (VDDCORE), U1.K9 (VDDCORE), U1.L7 (VDDCORE), U1.N6 (VDDCSI)
/Power_Unit/VDDSMPS: C7.1, C8.1, C9.1, C10.1, C11.1, C12.1, L2.1, U1.H1 (VDDSMPS), U1.H2 (VDDSMPS), U1.H3 (VDDSMPS), U1.H4 (VDDSMPS)
/Power_Unit/VLXSMPS: FB2.1, U1.G1 (VLXSMPS), U1.G2 (VLXSMPS), U1.G3 (VLXSMPS), U1.G4 (VLXSMPS)
/Power_Unit/VREFP: C20.1, C21.1, J1.2, U1.M1 (VREF+)
GND: C1.1, C3.2, C4.2, C5.2, C7.2, C8.2, C9.2, C10.2, C11.2, C12.2, C13.2, C14.2, C15.2, C16.2, C17.2, C18.2, C19.2, C20.2, C21.2, C22.2, C23.2, C24.2, C25.2, C26.2, C27.2, C28.2, C29.2, C30.1, C31.2, C32.2, C33.2, C34.2, C35.2, C36.1, C37.2, C38.1, C39.1, C40.1, C41.1, C42.1, D1.2 (A), D2.1 (K), D3.1 (K), D7.3 (common), D8.3 (common), D9.3 (common), D10.3 (common), R3.2, R5.2, R7.2, R9.2, R12.2, U1.A14 (VSS), U1.E2 (VSSAPMU), U1.E7 (VSS), U1.F1 (VSSSMPS), U1.F2 (VSSSMPS), U1.F3 (VSSSMPS), U1.F4 (VSSSMPS), U1.F5 (VSSAON), U1.F10 (VSS), U1.H10 (VSS), U1.H11 (VSS), U1.K5 (VSS), U1.K10 (VSS), U1.M4 (VSSA), U1.N1 (VREF-), U1.P1 (VSS), U1.P14 (VSS), U2.2 (GND), U3.2 (GND), U4.2 (GND), U5.2 (GND), U6.4 (GND); also elsewhere on the board
unnamed: D2.2 (A), R18.2
unnamed: D3.2 (A), R19.2
unnamed: C1.2, U1.D1 (V08CAP)
unnamed: R1.2, R3.1, U2.4 (ADJ)
unnamed: R4.2, R5.1, U3.4 (ADJ)
unnamed: R6.2, R7.1, U4.4 (ADJ)
unnamed: R8.2, R9.1, U5.4 (ADJ)
unnamed: R11.2, R12.1, U6.5 (CII)
unnamed: L3.1, U6.2 (SWE)
unnamed: C37.1, U6.3 (TC)
VDD: C13.1, C14.1, C15.1, C16.1, C17.1, C18.1, C19.1, C38.2, D1.1 (K), L3.2, R2.1, R2.2, R11.1, R18.1, U1.C2 (VBAT), U1.E8 (VDDIO4), U1.E9 (VDDIO4), U1.G10 (VDD), U1.G11 (VDD), U1.G12 (VDD), U1.J10 (VDDIO3), U1.J11 (VDDIO3); also elsewhere on the board
VDD1V8: C39.2, FB1.2, L2.2, R6.1, U4.5 (VOUT)
VDD3V3: C29.1, C42.2, R8.1, U1.A4 (VDD33USB), U5.5 (VOUT); also elsewhere on the board
VDDA1V8: C31.1, C32.1, C33.1, C34.1, C41.2, J1.1, R4.1, U1.D4 (VDDA18USB), U1.L4 (VDDA18PLL), U1.M3 (VDDA18ADC), U1.P5 (VDDA18CSI), U3.5 (VOUT)
VDDA1V8_AON: C22.1, C40.2, R1.1, R19.1, U1.E5 (VDDA18AON), U2.5 (VOUT); also elsewhere on the board

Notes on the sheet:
Global/Hierarchical Labels
Bypass Capacitors and Connectors
- VDD has 7 capacitors because: - 3 VDD pins - 2 VDDIO3 pins - 2 VDDIO4 pins - VDDCORE has 6 capacitors because: - 5 VDDCORE pins - 1 VDDCSI pin - VDDA1V8 has 4 capacitors because: - Powering ADC, USB, PLL, and CSI - Power input to BOARD is 5V @ 3A max - Total of 5 LDOs and Bucks for 3v3 and 1v8 - 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
Design Notes
STM32N6 Power Unit
Power Supplies



Board: 6 copper layers, 82.0 x 78.7 mm, 146 parts (70 on the bottom side), 155 nets.

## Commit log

2026-01-19 Added BACKLOG and PROGRESS files, to track progress and major tasks
    - Added all foreseeable tasks to BACKLOG, much to be discussed.
    - Added tasks for the next month into PROGRESS.
    - NOTE: Update tasks and responsibilities in BACKLOG after discussion.
2026-01-20 Added documentation for STM32N6, MX25LM, and IS42
2026-01-20 Created KiCAD Project, and STM32N657I0 footprint
    - Footprint is complete, as per datasheet specs
    - Symbol library yet to be created
    [STM32N6_Board.kicad_pcb, STM32N6_Board.kicad_sch]
2026-01-20 Added footprints for IS42 and MX25, symbol for IS42
    - All taken from SnapEDA
2026-01-20 Updated PROGRESS.md
    - Added all footprints
    - Added symbol for IS42
    - Yet to create symbols for STM32 and MX25
2026-01-21 Added IS42S16800F-7TLI symbol
    - Yet to create STM32N6 symbol
    - Made a typo on previous commit, IS42 symbol just finished
    MX25LM symbol previously imported
    [STM32N6_Board.kicad_sch]
2026-01-21 Created first of 3 STM32 symbol units
    - Analog unit is complete and checked
    - IO unit and Power unit to be created
2026-01-21 Created second of 3 STM32 symbol units
    - Analog unit and GPIO unit is now complete and checked
    - Power unit yet to go
2026-01-22 Finished last STM32 symbol unit
    - STM32 Symbol now broken down into Analog, GPIO, and Power units
    - Yet to begin design of board.
    - Also yet to fix one footprint issue.
2026-01-22 Fixed an issue with previous BGA footprint
    - I assumed rows were alphabetical; STM32 rows omitted I and O.
2026-01-22 Updated one of the symbols to look a little cleaner
    - Specifically the STM32 analog unit.
2026-01-22 Created the inital schematic for the Power unit
    - Power unit schematic completed but NOT CHECKED.
    - Also, V_DDA1V8PMU must be connected to V_DD1V8 somehow through a
    ferrite
    [STM32N6_Board.kicad_sch]
2026-01-24 Completed and checked the Power unit of the schematic
    - Completed the schematic with LDOs and Bucks as needed
    - Double checked all netlists.
    - Added relevant datasheets
    [STM32N6_Board.kicad_sch]
2026-01-25 Added lots of stuff
    - Completed most of power schematic YET TO ADD PWR LEDS
    - Completed bus wiring of the GPIO unit
    - Completed wiring of XSPI NOR Flash
    - Beginning wiring of Analog unit next
    - Redrew MX25LM symbol since pin numbers didn't match up
    [Analog_Unit.kicad_sch, Connectors.kicad_sch, GPIO.kicad_sch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]
2026-01-26 Completed wiring of the Analog unit.
    - CSI and USB buses are created, yet to be connected with connectors
    - Next will be pin selection, and drawing in FMC SDRAM
    - Then will be routing GPIOs as buses, and connecting with connectors
    - Finally, board layout.
    [Analog_Unit.kicad_sch, Connectors.kicad_sch, GPIO.kicad_sch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]
2026-01-27 Added and Updated some stuff
    - Added layout guide for the IS42 SDRAM chip
    - Modified reset pins wiring (now only on one reset button)
    - Added design notes in docs/STM32N6/DesignNotes.md
    - Updated PROGRESS.md
    [Analog_Unit.kicad_sch, NOR_Flash.kicad_sch, STM32N6_Board.kicad_sch]
2026-01-28 Completed ballout of STM32
    - Ballout completed using the STM32CubeMX software
    - Configuration is saved in a google spreadsheet, and a picture.
    - Config file will come soon.
2026-01-28 Added pinout to GPIO
    - Had to rearrange the pinout a little, due to SPI NSS issue
    - New pinout updated in google spreadsheet and image in docs
    - Added buses in GPIO sheet, as well as all necessary labels
    - Next is wiring in FMC SDRAM, and connectors.
    [Analog_Unit.kicad_sch, GPIO.kicad_sch, STM32N6_Board.kicad_sch]
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2026-02-04 Completed the schematic.
    - The schematic is complete.
    - ERC checker, footprint assignment, and PCB board design left
    [Analog_Unit.kicad_sch, Connectors.kicad_sch, FMC_SDRAM.kicad_sch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]
2026-02-04 Fixed a tiny issue
    [STM32N6_Board.kicad_sch]
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2026-02-04 Made fixes to remove ERC errors
    - 1 remaining error, but > 100 warnings D:
    - The remaining error is a bug within KiCAD I believe
    - Next is footprint assignment
    [Analog_Unit.kicad_sch, Connectors.kicad_sch, FMC_SDRAM.kicad_sch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]
2026-02-07 Completed schematic layout, ERC check, and footprint assignment
    - Completed and checked the schematic layout
    - Ran the ERC check; no errors (but lots of (checked) warnings)
    - Assigned footprints. Most in std lib, others in footprints.pretty
    - Imported the components to the PCB Editor, and fixed errors
    - All that's left is PCB layout!
    [Analog_Unit.kicad_sch, Connectors.kicad_sch, FMC_SDRAM.kicad_sch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]
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2026-02-16 Started the Main Board Design, added DigiPot datasheet.
    [mainboarddesign.kicad_pcb, mainboarddesign.kicad_sch]
2026-02-19 moved some stuff around
    [DWM1000.kicad_sch, ESP32S3.kicad_sch, Main_Board.kicad_pcb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]
2026-02-19 added 2 more sheets
    [Connectors.kicad_sch, ESP32S3.kicad_sch, Main_Board.kicad_sch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]
2026-02-19 Added buck converter datasheet, and symbols to project
    [Main_Board.kicad_pcb, Power.kicad_sch]
2026-02-26 Completed a lot of the layout of the STM Board
    - Major layout complete, but all the wiring still left. 488 open nets!
    - The STM32's BGA fanout is complete, now comes laying out traces
    [Analog_Unit.kicad_sch, Connectors.kicad_sch, FMC_SDRAM.kicad_sch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]
2026-02-27 Added bypass capacitors to the STM32
    [Analog_Unit.kicad_sch, Connectors.kicad_sch, FMC_SDRAM.kicad_sch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]
2026-03-21 Finished most of the Carrier Board. Few things left:
    - Need to add:
    - pin names
    - logo
    - datasheets
    [UWB_CarrierBoard.kicad_pcb, UWB_CarrierBoard.kicad_sch]
2026-03-21 Finished up the board, generated gerbers, and all other stuffs.
    - Added datasheets
    - Changed the TVS diode to smth JLC had in stock
    - Added pin labels
    - Obviously regenerated the gerbers n related stuff
    [UWB_CarrierBoard-B_Cu.gbl, UWB_CarrierBoard-B_Mask.gbs, UWB_CarrierBoard-B_Paste.gbp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]
2026-03-21 updated BOM and CPL
    [UWB_CarrierBoard_BOM.csv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]
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2026-03-27 Finished the SDRAM wiring
    [Analog_Unit.kicad_sch, Connectors.kicad_sch, FMC_SDRAM.kicad_sch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]
2026-03-27 added decoupling caps and other stuffs
    [Analog_Unit.kicad_sch, Connectors.kicad_sch, NOR_Flash.kicad_sch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]
2026-03-27 almost finished with the board
    [Analog_Unit.kicad_sch, Connectors.kicad_sch, GPIO.kicad_sch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]
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2026-03-27 Added the gerbers, drill files, BOM, and CPL files
    [Analog_Unit.kicad_sch, NOR_Flash.kicad_sch, Power_Unit.kicad_sch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]
2026-03-27 added datasheets for TVS diode, ferrite, and CSI FFC connector
2026-03-27 finished most of the main board
    [Connectors.kicad_sch, DWM1000.kicad_sch, ESP32S3.kicad_sch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]
2026-03-27 added gerbers, drill files, BOM and CPL for the main board
    [Connectors.kicad_sch, DWM1000.kicad_sch, ESP32S3.kicad_sch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]
